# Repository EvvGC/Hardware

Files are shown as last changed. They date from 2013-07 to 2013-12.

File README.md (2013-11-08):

EvvGC - Open Source 3 axis gimbal controller (hardware files)
======================

20130711 - initial creation and population of files

20130712 - updated vpre1.3ce2 with Digikey BOM, and a few part substitutions, no layout changes

20130712 - SandSquid link to the vpre1.3ce2 BOM - ~~http://www.sandsquid.com/#2FwTDG~~

20130714 - Updated vpre1.3ce2 componets R5, R13, R14 from 1k resistors to 10k to better match the STM spec

20130715 - No changes, just a quick sync of the 1.3ce2 documents and the OSH/Stencil file

20130802 - vpre1.3ce2 - SandSquid updated to include female housing/pins - ~~http://www.sandsquid.com/#b4xPP5~~

20130820 - vpre1.3ce2 - until further notice the online BOM on sandsquid isn't working... I'm working with the company to fix it
           they have some issues on their side

20130822 - vpre1.3ce2 - updated actual altium documents to reflect the resistor change on the green diodes.  Combined it with other 
           330ohm resistors so you'd only have to order more of the same as opposed a new line item.
         - updated the sandsquid BOM - link is ~~http://www.sandsquid.com/#wL1Nhu~~
         
20131107 - vpre1.3ce2 - updated XLS BOM file to reflect component changes for better heat distribution

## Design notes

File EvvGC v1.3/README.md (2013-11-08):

EvvGC v1.3
==================

Current version: vpre1.3ce2

SandSquid BOM link: ~~http://www.sandsquid.com/#wL1Nhu~~

20130820 - until further notice the sandsquid BOM above doesn't work.  I'm working with the sandsquid
           people to fix this. I'll update when I know more.
           
20130822 - updated actual altium documents to reflect the resistor change on the green diodes.  Combined it with other 
           330ohm resistors so you'd only have to order more of the same as opposed a new line item.
         - updated sandsquid BOM link to ~~http://www.sandsquid.com/#wL1Nhu~~

20131107 - updated XLS BOM file to reflect component changes for better heat distribution

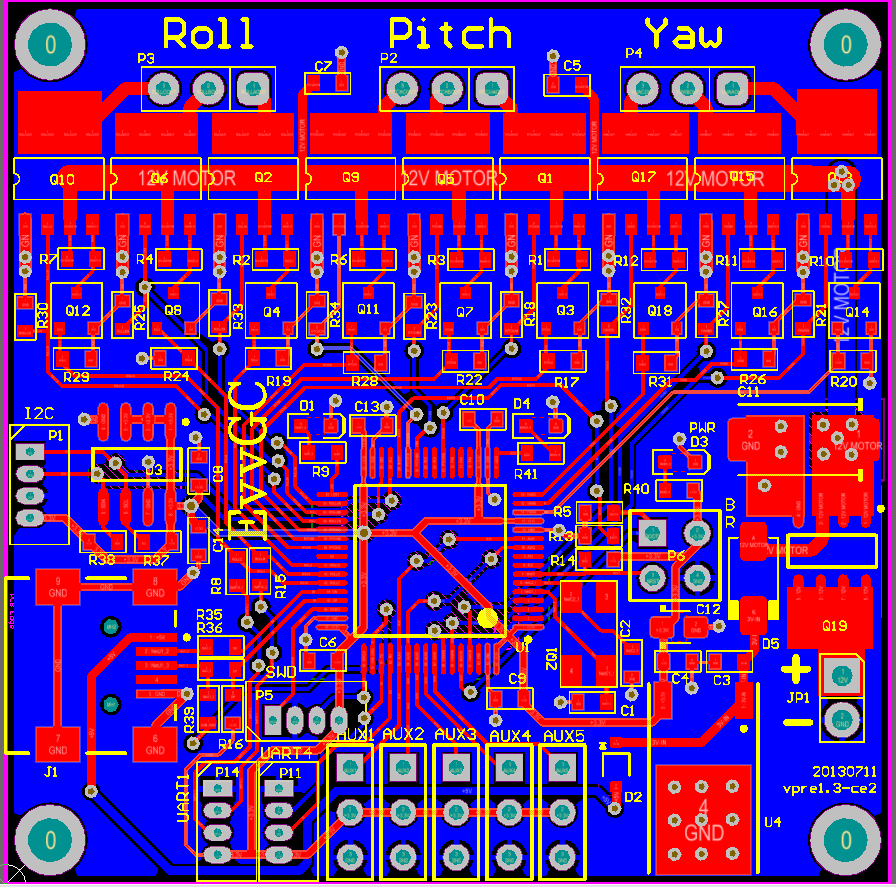
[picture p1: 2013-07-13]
EvvGC v1.3/ScreenShot.png

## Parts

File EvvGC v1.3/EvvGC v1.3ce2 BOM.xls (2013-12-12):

1.3ce2 BOM
Comment | Description | Designator | Footprint | Quantity | Digikey Part # | Digikey URL
0 | Resistor | C15/C16 | R-0603 | 2 | P0.0GCT-ND | http://www.digikey.com/product-detail/en/ERJ-3GEY0R00V/P0.0GCT-ND/134711
22 | Resistor | R35, R36 | R-0603 | 2 | P22.0HCT-ND | http://www.digikey.com/product-detail/en/ERJ-3EKF22R0V/P22.0HCT-ND/1746745
220 | Resistor | R39 | R-0603 | 1 | P220HCT-ND | http://www.digikey.com/product-detail/en/ERJ-3EKF2200V/P220HCT-ND/1746741
330 | Resistor | R9, R40, R41 | R-0603 | 3 | P330HCT-ND | http://www.digikey.com/product-detail/en/ERJ-3EKF3300V/P330HCT-ND/1746761
750 | Resistor | R1, R2, R3, R4, R6, R7, R10, R11, R12 | R-0603 | 9 | 541-750SCT-ND | http://www.digikey.com/product-detail/en/CRCW0603750RFKEAHP/541-750SCT-ND/2826037
1.5k | Resistor | R16 | R-0603 | 1 | P1.50KHCT-ND | http://www.digikey.com/product-detail/en/ERJ-3EKF1501V/P1.50KHCT-ND/198088
1k | Resistor | R8, R15 | R-0603 | 2 | P1.00KHCT-ND | http://www.digikey.com/product-detail/en/ERJ-3EKF1001V/P1.00KHCT-ND/198071
100nF | Capacitor | C3, C4, C5, C6, C7, C8, C9, C10, C13 | C-0603 | 9 | 478-1259-1-ND | http://www.digikey.com/product-detail/en/06033G104ZAT2A/478-1259-1-ND/564291
100uF25V | Capacitor Tantalum | C11 | CAPMP7343X310N | 1 | 399-8410-1-ND | http://www.digikey.com/product-detail/en/T491X107K025AT/399-8410-1-ND/3472133
10uF6.3V | Capacitor Tantalum | C12 | CAPMP2012X150USR | 1 | 478-3273-1-ND | http://www.digikey.com/product-detail/en/TAJR106K006RNJ/478-3273-1-ND/930065
10k | Resistor | R5, R13, R14, R17, R18, R19, R20, R21, R22, R23, R24, R25, R26, R27, R28, R29, R30, R31, R32, R33, R34 | R-0603 | 21 | P10.0KHCT-ND | http://www.digikey.com/product-detail/en/ERJ-3EKF1002V/P10.0KHCT-ND/198102
1uF | Capacitor | C14 | C-0603 | 1 | 478-5142-1-ND | http://www.digikey.com/product-detail/en/06033D105KAT2A/478-5142-1-ND/1913232
22pF | Capacitor | C1, C2 | C-0603 | 2 | 478-6200-1-ND | http://www.digikey.com/product-detail/en/06033A220JAT2A/478-6200-1-ND/2391399
4.7k | Resistor | R37, R38 | R-0603 | 2 | P4.70KHCT-ND | http://www.digikey.com/product-detail/en/ERJ-3EKF4701V/P4.70KHCT-ND/1746782
78M33 | Positive Voltage Regulator | U4 | TO-252 | 1 | 296-21208-1-ND | http://www.digikey.com/product-detail/en/UA78M33CKVURG3/296-21208-1-ND/1217113
8MHz | 7B-8.000MAAJ-T | ZQ1 | 7B_6x3.2 | 1 | 887-1452-1-ND | http://www.digikey.com/product-detail/en/7B-8.000MAAJ-T/887-1452-1-ND/2627020
APT1608QBC/D | LED Blue | D3 | LED-0603-BLUE | 1 | 754-1434-1-ND | http://www.digikey.com/product-detail/en/APT1608QBC%2FD/754-1434-1-ND/2163792
APT1608CGCK | LED Green | D1, D4 | LED-0603-GREEN | 2 | 754-1116-1-ND | http://www.digikey.com/product-detail/en/APT1608CGCK/754-1116-1-ND/1747833
Aux1 | Header, 3-Pin | P12 | HDR1X3 | 1
Aux2 | Header, 3-Pin | P13 | HDR1X3 | 1
Aux3 | Header, 3-Pin | P7 | HDR1X3 | 1
Aux4 | Header, 3-Pin | P9 | HDR1X3 | 1
Aux5 | Header, 3-Pin | P10 | HDR1X3 | 1
BOOT | Header, 2-Pin, Dual row | P6 | HDR2X2 | 1
BSS123 | N-channel Enhancement Mode Field-effect Transistor | Q3, Q4, Q7, Q8, Q11, Q12, Q14, Q16, Q18 | SOT-23 | 9 | BSS123NCT-ND | http://www.digikey.com/product-detail/en/BSS123/BSS123NCT-ND/244665
Header 3 | Header, 3-Pin | P2, P3, P4 | IDC1-3M | 3
I2C | 0530470410 | P1 | H53047-04 | 1 | WM1733-ND | http://www.digikey.com/product-search/en?WT.z_header=search_go&lang=en&site=us&x=23&y=15
FDS9435ACT | HEXFET Power MOSFET | Q19 | SO-8_N | 1 | FDS9435ACT-ND | http://www.digikey.com/product-detail/en/FDS9435A/FDS9435ACT-ND/965634
M24C02-WMN6TP | 2Kbit, 400kHz, 5V, I2C Serial EEPROM, 8-Pin SOIC 150mil, Extended Temperature | U3 | SOIC-SN8_N | 1 | 497-8552-1-ND | http://www.digikey.com/product-detail/en/M24C02-WMN6TP/497-8552-1-ND/2038654
1734035-2 | USB_Mini |  | USB-UX | 1 | A31727CT-ND | http://www.digikey.com/product-detail/en/1734035-2/A31727CT-ND/773789
POWER | Header, 2-Pin | JP1 | IDC1-2P | 1
SI4599DY | HEXFET Power MOSFET | Q1, Q2, Q5, Q6, Q9, Q10, Q13, Q15, Q17 | SO8-(SOT-96-1) | 9 | SI4599DY-T1-GE3CT-ND | http://www.digikey.com/product-detail/en/SI4599DY-T1-GE3/SI4599DY-T1-GE3CT-ND/2441968
SS14 | Diode | D2 | SOD323 | 1 | BAT760DICT-ND | http://www.digikey.com/product-detail/en/BAT760-7/BAT760DICT-ND/697116
SS14 | Diode | D5 | DO-214AC | 1 | SS14-E3/61TGICT-ND | http://www.digikey.com/product-detail/en/SS14-E3%2F61T/SS14-E3%2F61TGICT-ND/1091668
STM32F103RCT6 | STM32 ARM-based 32-bit MCU with 128 Kbytes Flash, 64-pin LQFP, Industrial Temperature | U1 | LQFP64_N | 1 | 497-9033-ND | http://www.digikey.com/product-detail/en/STM32F103RCT6/497-9033-ND/2035353
SWD | 0530470410 | P5 | H53047-04 | 1 | WM1733-ND | http://www.digikey.com/product-search/en?WT.z_header=search_go&lang=en&site=us&x=23&y=15
UART1 | 0530470410 | P14 | H53047-04 | 1 | WM1733-ND | http://www.digikey.com/product-search/en?WT.z_header=search_go&lang=en&site=us&x=23&y=15
UART4 | 0530470410 | P11 | H53047-04 | 1 | WM1733-ND | http://www.digikey.com/product-search/en?WT.z_header=search_go&lang=en&site=us&x=23&y=15
Female conn housing | 510210400 | P1, P5, P11, P14 | Housing | 4 | WM1722-ND | http://www.digikey.com/product-search/en?x=-1124&y=-73&lang=en&site=us&KeyWords=WM1722-ND
Female housing pins | 500798000 | P1, P5, P11, P14 | Pin | 16 | WM1142CT-ND | http://www.digikey.com/product-detail/en/0500798000/WM1142CT-ND/467835

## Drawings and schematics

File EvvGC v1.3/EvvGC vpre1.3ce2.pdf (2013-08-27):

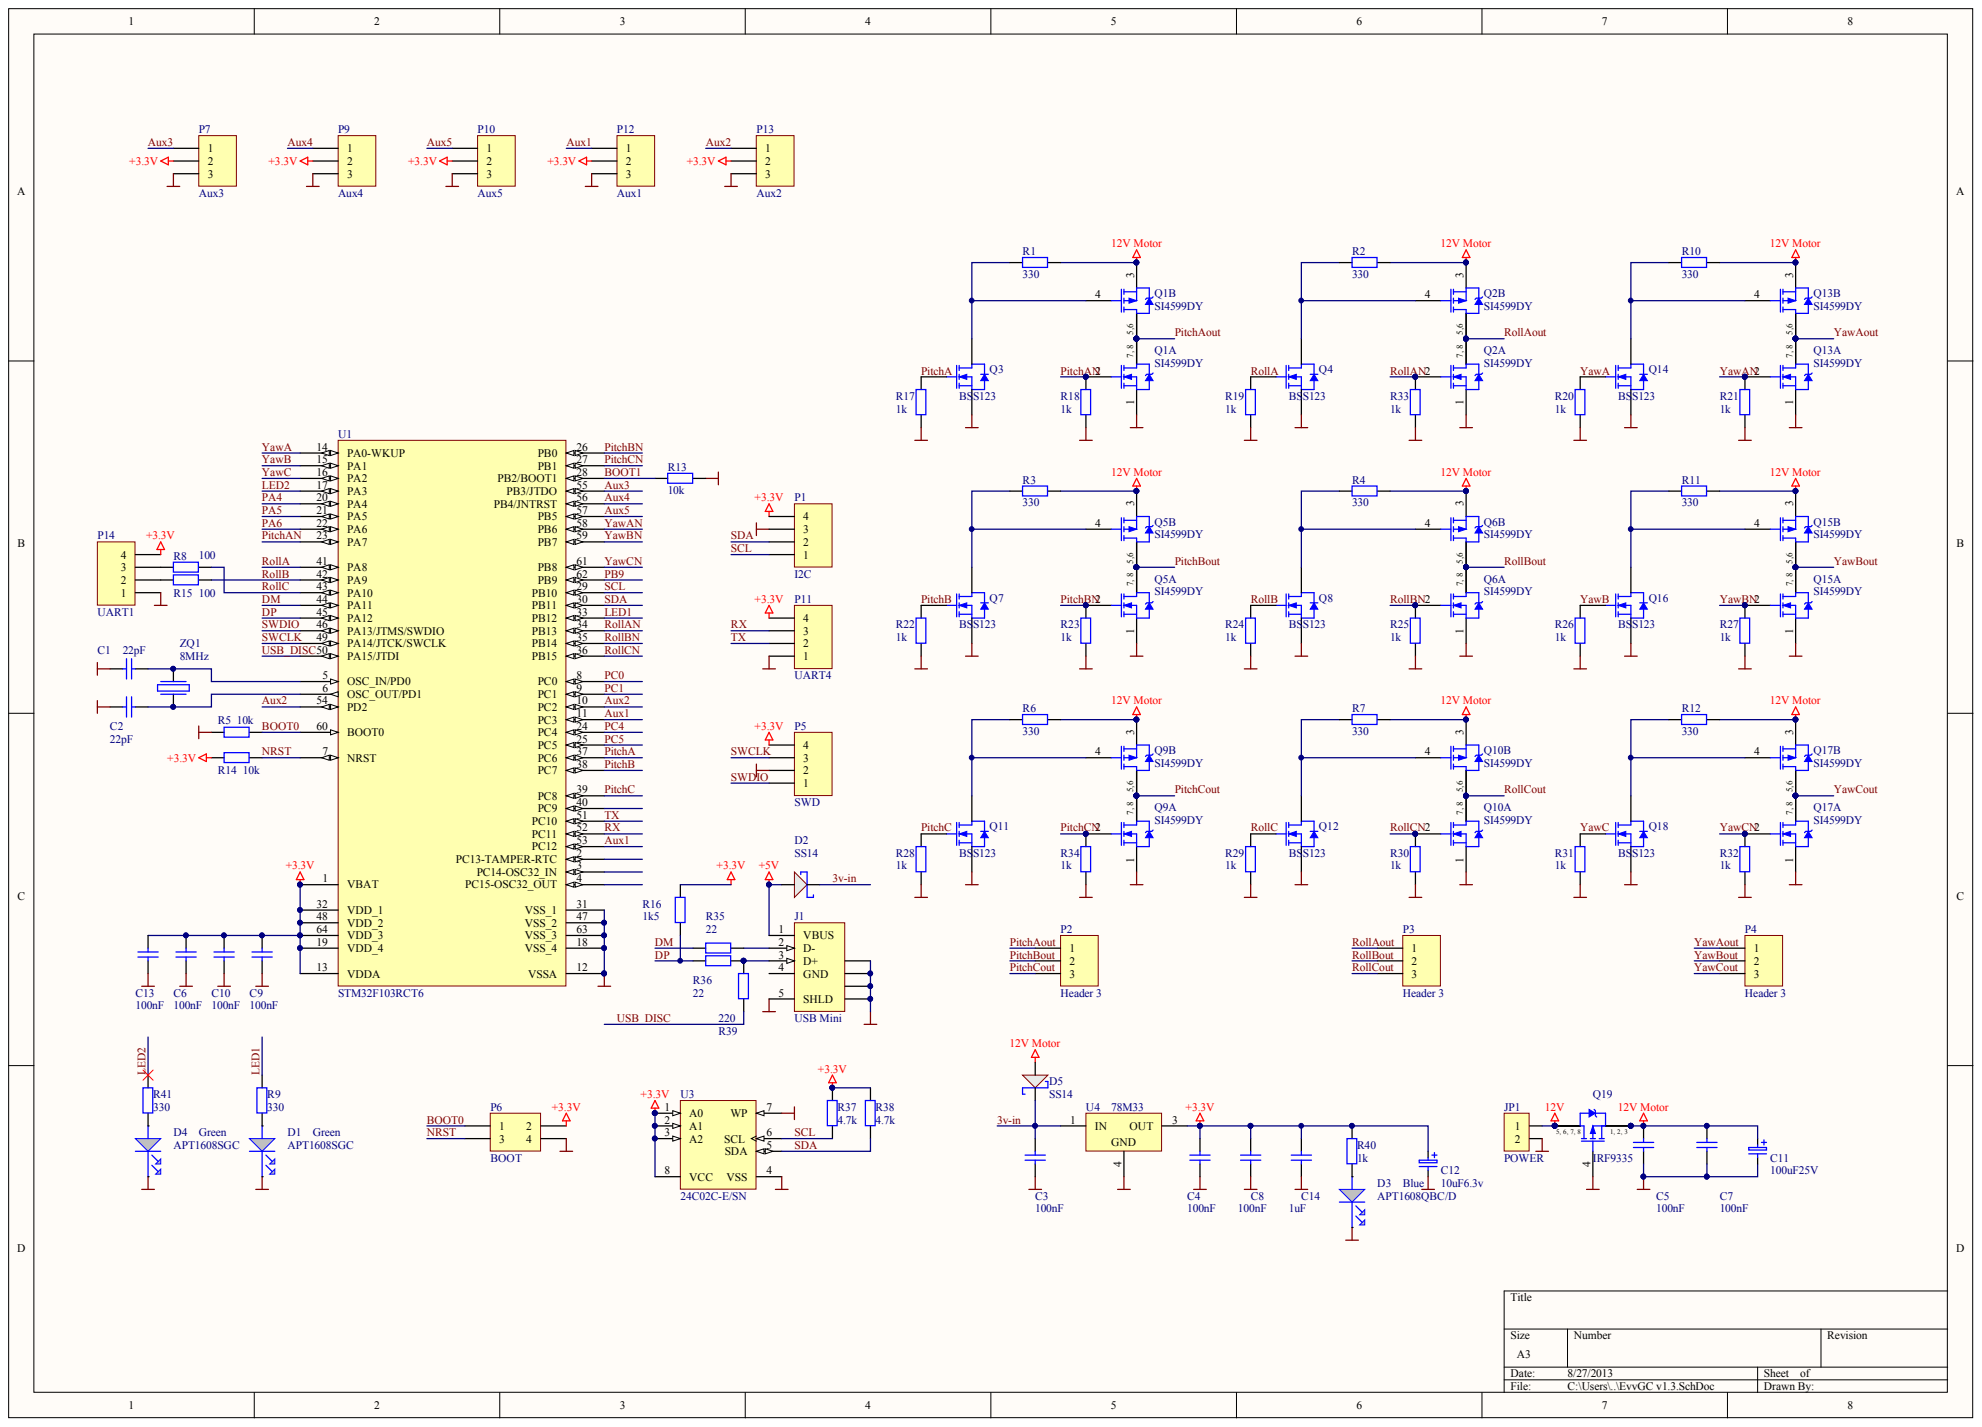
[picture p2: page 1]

RollB | PA9 42
RollC | PA10 43

OSC_OUT/PD1 6

Aux2 | PD2 54

Comment | Description | Designator | Footprint | LibRef | Quantity
22pF | Capacitor | C1, C2 | c-0603 | CAP0805 | 2
100nF | Capacitor | C3, C4, C5, C6, C7, C8, C9, C10, C13 | c-0603 | CAP0805 | 9
100uF25V | Capacitor Tantalum | C11 | CAPMP7343X310N | CT | 1
10uF6.3v | Capacitor Tantalum | C12 | CAPMP2012X150USR | CT | 1
1uF | Capacitor | C14 | c-0603 | CAP0805 | 1
APT1608SGC | APT1608SGC | D1, D4 | LED-0603-GREEN | LED | 2
SS14 | Diode | D2 | SOD323 | DIODE SCHOTTKY | 1
APT1608QBC/D | APT1608QBC/D | D3 | LED-0603-BLUE | LED | 1
SS14 | Diode | D5 | DO-214AC | DIODE SCHOTTKY | 1
USB Mini | USB 2.0, Right Angle, SMT, B Type, Receptacle, 5 Position, Black | J1 | 440247 | 440247-2 | 1
POWER | Header, 2-Pin | JP1 | IDC1-2P | CON2 | 1
I2C | 0530470410 | P1 | H53047-04 | Header 4 | 1
Header 3 | Header, 3-Pin | P2, P3, P4 | IDC1-3M | Header 3 | 3
SWD | 0530470410 | P5 | H53047-04 | Header 4 | 1
BOOT | Header, 2-Pin, Dual row | P6 | HDR2X2 | Header 2X2 | 1
Aux3 | Header, 3-Pin | P7 | HDR1X3 | Header 3 | 1
Aux4 | Header, 3-Pin | P9 | HDR1X3 | Header 3 | 1
Aux5 | Header, 3-Pin | P10 | HDR1X3 | Header 3 | 1
UART4 | 0530470410 | P11 | H53047-04 | Header 4 | 1
Aux1 | Header, 3-Pin | P12 | HDR1X3 | Header 3 | 1
Aux2 | Header, 3-Pin | P13 | HDR1X3 | Header 3 | 1
UART1 | 0530470410 | P14 | H53047-04 | Header 4 | 1
SI4599DY | HEXFET Power MOSFET | Q1, Q2, Q5, Q6, Q9, Q10, Q13, Q15, Q17 | SO8-(SOT-96-1) | AUIRF7343 | 9
BSS123 | N-channel Enhancement Mode Field-effect Transistor | Q3, Q4, Q7, Q8, Q11, Q12, Q14, Q16, Q18 | SOT-23 | 2N7002 | 9
IRF9335 | HEXFET Power MOSFET | Q19 | SO-8_N | IRF7404 | 1
330 | Resistor | R1, R2, R3, R4, R6, R7, R9, R10, R11, R12, R41 | r-0603 | Res, Res, Res, Res, Res, Res, RES 0603 330R, Res, Res, Res, RES 0603 330R | 11
10k | Resistor | R5, R13, R14 | R-0603 | RES 0603 330R | 3
100 | Resistor | R8, R15 | R-0603 | RES 0603 330R | 2
1k5 | Resistor | R16 | R-0603 | RES 0603 330R | 1
1k | Resistor | R17, R18, R19, R20, R21, R22, R23, R24, R25, R26, R27, R28, R29, R30, R31, R32, R33, R34, R40 | r-0603 | Res, Res, Res, Res, Res, Res, Res, Res, Res, Res, Res, Res, Res, Res, Res, Res, Res, Res, RES 0603 330R | 19
22 | Resistor | R35, R36 | R-0603 | RES 0603 330R | 2
4.7k | Resistor | R37, R38 | R-0603 | RES 0603 330R | 2
220 | Resistor | R39 | r-0603 | Res | 1
STM32F103RCT6 | STM32 ARM-based 32-bit MCU with 128 Kbytes Flash, 64-pin LQFP, Industrial Temperature | U1 | LQFP64_N | STM32F103RBT6 | 1
24C02C-E/SN | 2Kbit, 400kHz, 5V, I2C Serial EEPROM, 8-Pin SOIC 150mil, Extended Temperature | U3 | SOIC-SN8_N | 24C02C-E/SN | 1
78M33 | Positive Voltage Regulator | U4 | TO-252 | L78M05CDT | 1
8MHz | 7B-8.000MAAJ-T | ZQ1 | 7B_6x3.2 | ZQ_KX12B | 1

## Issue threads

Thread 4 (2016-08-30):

Gate drive resistors overheating.

lberezy, 2016-08-30:
The resistors R1, R3, R6 etc attached to the high side of the gate drive mosfets BSS123 appears to be incapable of dissipating the required heat generated. Each of these 330 Ohm resistors is dropping around 11.8 V across it, or close to 38 mA. This means that 0.038^2 * 330 = 477 mW of power is being dissipated by these resistors. 0603 package resistors should only be handling 100 mW MAX power.

Is there a reason why this resistor was chosen so low or the package size incorrectly picked? Sizing the resistor up to 1210 package brings the thermal problem under control, but is obviously sub-optimal. Increasing the resistance to above 1.5k Ohm reduces the current such that it is under 100 mW dissipated.

Please advise.

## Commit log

2013-07-11 added files and directories
    [EvvGC v1.1.PcbDoc, EvvGC v1.1.PrjPcb, EvvGC v1.1.SchDoc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]
2013-07-13 updated vpre1.3ce2 with BOM, slight part changes added Stencil files
    [EEvvGC v1.3ce2 BOM.xls, EvvGC v1.3.PcbDoc, EvvGC v1.3.PrjPcb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]
2013-07-13 Update README.md
    added sandsquid link to BOM
2013-07-15 vpre1.3ce2 - updated BOM to replace R5, R13, R14 with a 10k from original specified 1k to better match STM specification
    [EEvvGC v1.3ce2 BOM.xls, EvvGC v1.3.PcbDoc, EvvGC v1.3.SchDoc]
2013-07-15 refresh of zip files for OSH/Stencil - no changes
    [EvvGC v1.3.PcbDoc]
2013-08-02 Update README.md
    Added female Molex picoBlade female housing/pins to sandsquid BOM
2013-08-02 Update README.md
    Updated SandSquid link with female Molex picoBlade housing/pins
2013-08-21 Removed sandsquid BOM link, updated 1.3 XLS BOM
    [EEvvGC v1.3ce2 BOM.xls, EvvGC v1.3ce2 BOM.xls]
2013-08-22 updated BOM to use 330 ohm resistor for R9 and R41, instead of a new 294ohm one - combined to another already in use
    [EvvGC v1.3ce2 BOM.xls]
2013-08-22 modified vpre1.3ce2 for the resistor change on the green diodes
    [EvvGC v1.3.PcbDoc, EvvGC v1.3.PrjPcb, EvvGC v1.3.SchDoc]
2013-08-22 Update README.md
    Updated sandsquid BOM link for vpre1.3ce2 BOM
2013-08-22 Update README.md
    Updated sandsquid BOM link
2013-08-27 updated pdf to include schematic instead of board view
2013-08-29 Update README.md
    updated link to sandsquid BOM
2013-11-08 updated 1.3 BOM to reflect component changes for better heat distribution
    [EvvGC v1.3ce2 BOM.xls]
2013-12-12 more component changes to the BOM
    [EvvGC v1.3ce2 BOM.xls]
